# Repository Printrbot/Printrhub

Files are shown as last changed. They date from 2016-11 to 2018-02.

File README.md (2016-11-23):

# Printrhub

Welcome and thank you for your interest in our Printrhub technology. In this repository you will find everything you need to build upon the technology we invented. You may use the code and hardware to build your own devices or to improve your own Simple 2016. Please let us know about your projects and post issues or pull request to help us improve this project and code base.

## Purpose of the Printrhub

The Printrhub is the display component of our 3D printer Simple 2016 (http://printrbot.com/new-2016-simple/) and thus is the main user interface. The user can select, start, modify and pause prints or setup the printer with it. A fluid user interface controlled by touch as you know it from your smartphone let's anyone can start a print. The Hub also controls the printer and handles communication with the Printrbot cloud.

The Printrhub contains these components that form the final hardware

* ESP-12E module for WiFi connection and Over the Air updates
* MK20DX256LHV7 (Teensy 3) MCU is the main processor for handling the display, touch, SD card, controls the printer and ESP-12E
* 2.8 inch TFT display with 320x240 pixels
* Capacitive touch screen
* microSD card slot

As our board hosts two MCUs we need two different firmware, one for the ESP-12E module and the other one for the main MCU.

## Organization of this repository

* **/esp**: The firmware for the ESP-12E WiFi module
* **/mk20**: Contains the firmware for the main processor
* **/pcb**: Revisions 0.1, and 0.4 (final revision) of the PCB as Eagle and Copper files (for BOM and 3D views)
* **/utils**: The image tool that we use to build the ui.min file that contains all images used by the firmware combined in one file
* **/sdcard**: The initial content of the SD card that we ship with your printer (contains firmware images and root folder structure)
 
## Documentation
  
We have developed the hub in cooperation with Phillip Schuster (http://www.appfruits.com). He has written some documentation and behind the scenes reports that you should have read before working with our code and hardware.

### Behind the scenes of the Printrbot Simple 2016

How we started development and why we think you will learn something about product development in general.
http://www.appfruits.com/2016/11/behind-the-scenes-printrbot-simple-2016/

### Display System Explained

Expains the display and application framework in great detail. Explains the application flow, how to pseudo code multi threading and how implement a fast fluid and responsive user interface in a device capable of only 64 KB of RAM and 72 MHz.
http://www.appfruits.com/2016/11/printrbot-simple-2016-display-system-explained/

### CommStack explained

We invented CommStack to handle the communication between the MK20 and the ESP-12E module. It's fast, robust, bidirectional and features a nice request/response based system that enables two or more MCUs to communicate without having to handle all the little details.
http://www.appfruits.com/2016/11/printrbot-simple-2016-commstack-explained/

### Hardware explained

Describes the hardware in detail. Provides schematics, layout and details about the hardware we developed for the Printrbot hub.
http://www.appfruits.com/2016/11/printrbot-simple-2016-hardware-pcb-explained/

## Credits

Contains code or portions from these great libraries

* https://github.com/bakercp/PacketSerial
* https://github.com/PaulStoffregen/ILI9341_t3
* https://github.com/PaulStoffregen/ILI9341_fonts
* https://github.com/scanlime/esp8266-arm-swd
* https://github.com/esp8266/Arduino
* https://github.com/me-no-dev/ESPAsyncTCP.git
* https://github.com/me-no-dev/ESPAsyncWebServer.git
* https://github.com/bblanchon/ArduinoJson.git

Developed in cooperation with Phillip Schuster (@appfruits) from Appfruits (http://www.appfruits.com). Big thanks to Paul J. Stoffregen (https://www.pjrc.com/teensy/index.html) and his amazing Teensy project. It served as a great starting point and his amazing display driver for ILI9341 based display made our modern, fluid user interface possible.

## Support us

Printrbot invests time and resources providing this open source code, please support Printrbot and open-source hardware by purchasing products from Printrbot (http://www.printrbot.com)!

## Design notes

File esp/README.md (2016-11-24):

# Firmware for ESP-12E module

Printrhub consists of two MCUs on one board. The first is the well know ESP-8266 MCU, implemented as a ESP-12E module on the PCB. The second MCU is MK20DX256VLH7, better known as Teensy 3.1/3.2.

ESP is responsible for these features:

* Flashes MK20 MCU with latest firmware using ARMs SWD protocol
* Requests and downloads from the web
* Initial setup with WiFi and connecting your printer to the Printrbot Cloud

You will find the firmware for the ESP module on Printrhub board in this folder (esp). This is what you need to compile and install the firmware:

* Latest PlatformIO IDE (http://platformio.org)
* CLion (optional) (https://www.jetbrains.com/clion/)
* FTDI cable to transfer firmware to ESP module (for example this one https://www.sparkfun.com/products/9873)

## Getting started

Connect the FTDI header to the connection port marked FTDI on Printrhub and make sure it's connected in the right direction. If you use Sparkfuns FTDI breakout the IC on the breakout board should point to the Printrhub board.

## Uploading firmware to ESP

Before uploading the ESP firmware you will need to set ESP in DFU mode. You will need to do that before each upload cycle.

Press and hold the button named GPIO0 on the Printrhub board and press the RESET button on the Printrhub board. Release the GPIO0 button. The small LED on the bottom right side of the Printrhub should lightly dim now
indicating ESP is in DFU mode now.

## Using PlatformIO IDE to compile and upload ESP firmware

Download the latest PlatformIO IDE and install it. Open the esp folder in your PlatformIO IDE and compile the code. 

Make sure PlatformIO IDE uses the right USB connection (to the FTDI cable or breakout board) and upload the code. It will take some time.

## Using CLion to compile and upload ESP firmware

It's possible to use the awesome CLion IDE and we internally used that for development. CLion will use PlatformIO in the background but will seamlessly integrate it. You get a superior IDE but without the CMake hassle.
After you have installed PlatformIO and CLion open a terminal and navigate to this esp folder. Use this command to let PlatformIO setup a CLion IDE project for you.

`platformio init --ide clion --board esp12e`

Open the folder esp in CLion and you should have a nice, already setup project in CLion. Use the different targets available like PLATFORMIO_BUILD to compile the project and PLATFORMIO_UPLOAD to build and upload the project. 
Use the Build command to run the target process. Before uploading make sure your FTDI cable/breakout board is connected and ESP is in DFU mode (see above).

## Initial setup

If you applied the firmware you should see a new WiFi network named "Printrbot" on your phone or Mac/PC. Connect to that and open http://printrbot.local in your browser. You should see an initial setup screen
where you can enter your WiFi credentials of your local network.

Once that is done, ESP restarts and tries to connect to the local network. Wait a few minutes as ESP will detect that MK20 does not have a firmware installed and will automatically dowmload the latest MK20 firmware
from the web and flash MK20. After about 3-4 minutes Printrhub display will turn on and Printrhub is ready to explore

## Special considerations

ESP and MK20 use a direct connection based on UART and a custom protocol that we developed: CommStack. As CommStack uses the same Serial connection as FTDI cable uses to upload the firmware it's sometimes necessary to
 keep MK20 disabled while uploading the firmware. If you get strange upload errors and are sure ESP module is in DFU mode you have to short RESET_B (named RES_B on the Printrhub board) to GND. It's easy to do that as
 Printrhub has test points you can use to do that. If you do more constant development you should solder a wire to RES_B and GND and connect them together before uploading a firmware to ESP.
 
 MK20 detects if you want to upload a firmware to ESP by sensing the GPIO0 signal and stop any Serial communication through CommStack, but if MK20 firmware is not running correctly which can sometimes happen during 
 development you will have to stop it running.

## Support

There is no official support for this, but please drop an Issue and we'll have a look.

## License

Copyright (c) 2016 Printrbot Inc.

Permission is hereby granted, free of charge, to any person obtaining a copy of this software and associated documentation files (the "Software"), to deal in the Software without restriction, including without limitation 
the rights to use, copy, modify, merge, publish, distribute, sublicense, and/or sell copies of the Software, and to permit persons to whom the Software is furnished to do so, subject to the following conditions:

The above copyright notice and this permission notice shall be included in all copies or substantial portions of the Software.

THE SOFTWARE IS PROVIDED "AS IS", WITHOUT WARRANTY OF ANY KIND, EXPRESS OR IMPLIED, INCLUDING BUT NOT LIMITED TO THE WARRANTIES OF MERCHANTABILITY, FITNESS FOR A PARTICULAR PURPOSE AND NONINFRINGEMENT. IN NO EVENT SHALL THE 
AUTHORS OR COPYRIGHT HOLDERS BE LIABLE FOR ANY CLAIM, DAMAGES OR OTHER LIABILITY, WHETHER IN AN ACTION OF CONTRACT, TORT OR OTHERWISE, ARISING FROM, OUT OF OR IN CONNECTION WITH THE SOFTWARE OR THE USE OR OTHER DEALINGS IN THE SOFTWARE.

## Credits

Contains code or portions from these great libraries

* https://github.com/scanlime/esp8266-arm-swd
* https://github.com/bakercp/PacketSerial
* https://github.com/esp8266/Arduino
* https://github.com/me-no-dev/ESPAsyncTCP.git
* https://github.com/me-no-dev/ESPAsyncWebServer.git
* https://github.com/bblanchon/ArduinoJson.git

Developed in cooperation with Phillip Schuster (@appfruits) from Appfruits (http://www.appfruits.com).

## Support us

Printrbot invests time and resources providing this open source code, please support Printrbot and open-source hardware by purchasing products from Printrbot (http://www.printrbot.com)!

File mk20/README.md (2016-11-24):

# Firmware for MK20DX256LHV7 (Teensy 3.x) MCU

Printrhub consists of two MCUs on one board. The first is the well know ESP-8266 MCU, implemented as a ESP-12E module on the PCB. The second MCU is MK20DX256VLH7, better known as Teensy 3.1/3.2.

Teensy MCU is responsible for these features:

* Reads and writes from SD card
* Controls Display, Touch and printer
* Communicates with ESP-12E module to download project index files and G-Codes from Printrbot cloud

You will find the firmware for the MCU on Printrhub board in this folder (mk20). This is what you need to compile and install the firmware:

* Latest PlatformIO IDE (http://platformio.org)
* CLion (optional) (https://www.jetbrains.com/clion/)
* Segger J-LINK or similar SWD compatible debug probe

## Documentation

One of our team members has written an extensive documentation and behind the scenes report about the development of the Printrbot Simple 2016. We advise you to read this before digging into this code to give you some context and advise.

### Behind the scenes of the Printrbot Simple 2016

How we started development and why we think you will learn something about product development in general.
http://www.appfruits.com/2016/11/behind-the-scenes-printrbot-simple-2016/

### Display System Explained

Expains the display and application framework in great detail. Explains the application flow, how to pseudo code multi threading and how implement a fast fluid and responsive user interface in a device capable of only 64 KB of RAM and 72 MHz.
http://www.appfruits.com/2016/11/printrbot-simple-2016-display-system-explained/

### CommStack explained

We invented CommStack to handle the communication between the MK20 and the ESP-12E module. It's fast, robust, bidirectional and features a nice request/response based system that enables two or more MCUs to communicate without having to handle all the little details.
http://www.appfruits.com/2016/11/printrbot-simple-2016-commstack-explained/

### Hardware explained

Describes the hardware in detail. Provides schematics, layout and details about the hardware we developed for the Printrbot hub.
http://www.appfruits.com/2016/11/printrbot-simple-2016-hardware-pcb-explained/

## Using PlatformIO IDE to compile MK20 firmware

Download the latest PlatformIO IDE and install it. Open the mk20 folder in your PlatformIO IDE and compile the code. 

## Uploading firmware

There are two options to upload new firmware to the device:

* Using existing over the air update mechanism (see ESP firmware in this repository)
* SWD compatible ARM debug probe (like Segger J-LINK) to upload code via Serial Wire Debug (SWD)
  
### Over the Air updates
  
  If you don't have the necessary hardware (debug probe) to upload code via SWD then this is the easiest method. You will need to modify the ESP firmware. This is an excerpt of the file web_server.cpp and sets up a GET request that is watching for a /update_mk20 event and starts a firmware update. 
  
  ```
    webserver.addOptionsRequest("/update_mk20");
    server.on("/update_mk20", HTTP_GET, [](AsyncWebServerRequest *request) {
  	String mk20FirmwareFile("/mk20.bin");
  	FirmwareUpdateInfo *updateInfo = Application.getFirmwareUpdateInfo();
  	if (updateInfo != NULL) {
  	  DownloadFileToSPIFFs *downloadMK20Firmware = new DownloadFileToSPIFFs(updateInfo->mk20_url, mk20FirmwareFile);
  	  MK20FirmwareUpdate *mk20UpdateFirmware = new MK20FirmwareUpdate(mk20FirmwareFile);
  	  downloadMK20Firmware->setNextMode(mk20UpdateFirmware);
  	  Application.pushMode(downloadMK20Firmware);
  	  request->send(200, "text/plain", "\nupdate of MK20 started, please wait...\n\n");
  	} else {
  	  request->send(200, "text/plain", "\nupdate of MK20 failed, please wait until firmware data have been loaded and try again...\n\n");
  	}
    });
  ```
  
  However, this code loads the firmware provided by the Printrbot Cloud. You will want to user your own binary file. Best way is to modify it this way:
   
     ```
       webserver.addOptionsRequest("/update_mk20");
       server.on("/update_mk20", HTTP_GET, [](AsyncWebServerRequest *request) {
     	String mk20FirmwareFile("/mk20.bin");
     	FirmwareUpdateInfo *updateInfo = Application.getFirmwareUpdateInfo();
     	if (updateInfo != NULL) {
     	  DownloadFileToSPIFFs *downloadMK20Firmware = new DownloadFileToSPIFFs("http://WWW.YOURDOMAIN.COM/YOURFIRMWARE.BIN", mk20FirmwareFile);
     	  MK20FirmwareUpdate *mk20UpdateFirmware = new MK20FirmwareUpdate(mk20FirmwareFile);
     	  downloadMK20Firmware->setNextMode(mk20UpdateFirmware);
     	  Application.pushMode(downloadMK20Firmware);
     	  request->send(200, "text/plain", "\nupdate of MK20 started, please wait...\n\n");
     	} else {
     	  request->send(200, "text/plain", "\nupdate of MK20 failed, please wait until firmware data have been loaded and try again...\n\n");
     	}
       });
     ```
     
     This will use the standard over the air updates but will use the URL you provide to flash MK20.
     
The workflow would be this:
     
     * Compile MK20 firmware and generate a bin file from the hex file (see hextobin.sh) for details on how to do that
     * Upload your firmware binary to your own webspace or local webserver
     * Modify ESP firmware and flash ESP
     * Load this URL in your browser to receive some helful logs (http://IPADDRESS_OF_PRINTER/events)
     * Start up your printer and call this URL in your browser (http://IPADDRESS_OF_PRINTER/update_mk20)
     * ESP will download your firmware and install it. Your display will turn off.
     
### Uploading code via SWD
      
If you want to upload via SWD connect your probe to SWD_IO, SWD_CLK, GND and RESET_B. You will also need to connect your VREF to 3.3V. This way your debug probe can sense the correct logic level. See your manual for details on the procedure. All necessary signals are exposed in the test points in the middle of the board.

## Using CLion to compile and upload ESP firmware

It's possible to use the awesome CLion IDE and we internally used that for development. CLion will use PlatformIO in the background but will seamlessly integrate it. You get a superior IDE but without the CMake hassle. After you have installed PlatformIO and CLion open a terminal and navigate to this mk20 folder. Use this command to let PlatformIO setup a CLion IDE project for you.

`platformio init --ide clion`

Open the folder mk20 in CLion and you should have a nice, already setup project in CLion. Use the different targets available like PLATFORMIO_BUILD to compile the project. Use the Build command to run the target process. 

You will need 2016.2 or the latest 2016.3 of CLion for remote debugging via SWD. 

## Support

There is no official support for this, but please drop an Issue and we'll have a look. If you find bugs or add enhancements, please let us know and send a pull request.

## License

Copyright (c) 2016 Printrbot Inc.

Permission is hereby granted, free of charge, to any person obtaining a copy of this software and associated documentation files (the "Software"), to deal in the Software without restriction, including without limitation 
the rights to use, copy, modify, merge, publish, distribute, sublicense, and/or sell copies of the Software, and to permit persons to whom the Software is furnished to do so, subject to the following conditions:

The above copyright notice and this permission notice shall be included in all copies or substantial portions of the Software.

THE SOFTWARE IS PROVIDED "AS IS", WITHOUT WARRANTY OF ANY KIND, EXPRESS OR IMPLIED, INCLUDING BUT NOT LIMITED TO THE WARRANTIES OF MERCHANTABILITY, FITNESS FOR A PARTICULAR PURPOSE AND NONINFRINGEMENT. IN NO EVENT SHALL THE 
AUTHORS OR COPYRIGHT HOLDERS BE LIABLE FOR ANY CLAIM, DAMAGES OR OTHER LIABILITY, WHETHER IN AN ACTION OF CONTRACT, TORT OR OTHERWISE, ARISING FROM, OUT OF OR IN CONNECTION WITH THE SOFTWARE OR THE USE OR OTHER DEALINGS IN THE SOFTWARE.

## Credits

Contains code or portions from these great libraries

* https://github.com/bakercp/PacketSerial
* https://github.com/PaulStoffregen/ILI9341_t3
* https://github.com/PaulStoffregen/ILI9341_fonts

Developed in cooperation with Phillip Schuster (@appfruits) from Appfruits (http://www.appfruits.com).

## Support us

Printrbot invests time and resources providing this open source code, please support Printrbot and open-source hardware by purchasing products from Printrbot (http://www.printrbot.com)!

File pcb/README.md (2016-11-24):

# Printrhub PCB

This repository contains two revisions of the PCB of the Printrhub. See main folder for more details about the project.

## Documentation and details

This PCB has been developed in cooperation by Phillip Schuster (http://www.appfruits.com). He has written a blog post about these PCBs and documents the details of it.
http://www.appfruits.com/2016/11/printrbot-simple-2016-hardware-pcb-explained/

## Revisions

This folder contains two revisions:

### Revision 0.1

This has been the first PCB we have created and contains the Teensy bootloader chip and an USB port that makes it easy to flash new firmware. It's basically just a bigger Teensy with more components. The firmware supports this revision, but you will need to set the correct #define in the HAL.h file in both firmwares

### Revision 0.4

This is the final revision we ship with the Simple 2016. Firmware must be flashed via SWD or our Over the Air update system.

## EAGLE and Copper files

These files can be opened with EAGLE, but you will need at least a Hobbyist license as we use 4-layers. We have also added Copper (http://www.copper-app.com) files that contain the complete BOM and a 3D view of the boards.

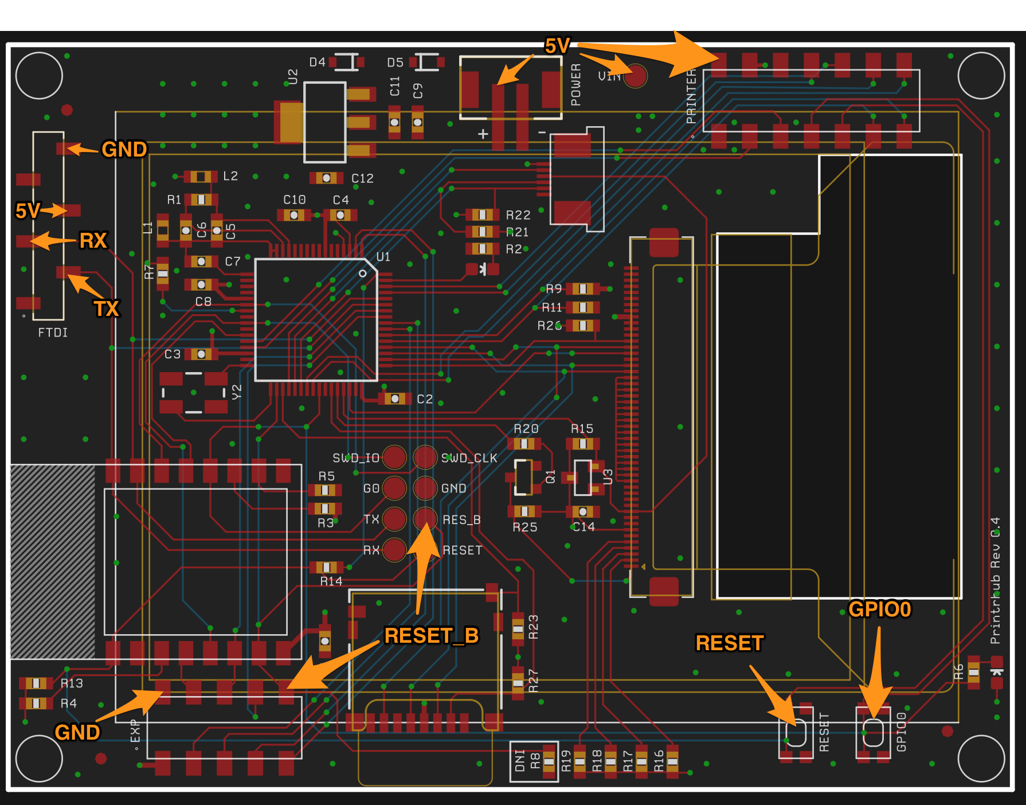
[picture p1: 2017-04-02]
Signals.png

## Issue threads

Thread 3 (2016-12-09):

Info button / display settings for part preview

ururk, 2016-12-09:
Currently, the only way to know what the settings are for a part on the printer is to hit print - it would be useful to have an info button that displays the basic information for a part (essentially, whatever options are configurable), including print time and filament quantity. An uncluttered preview is nice - hence an info button. The current UI is nicely done, and this is just a suggestion.

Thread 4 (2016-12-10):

add git tags for firmware release numbers.

bmv437, 2016-12-10:
Hi there. I can see that my printrhub has firmware package 108, but I'm not sure at what commit that firmware package was built. Is it possible to add git tags so we can keep track of what code gets shipped in which firmware build?

```json
{
    "firmware": 108,
    "fw_cloud_buildnr": 108,
    "fw_info_sent": true,
    "fw_update": true,
    "ipaddress": "192.168.1.10",
    "locked": false,
    "mk20": true,
    "name": "printrbot",
    "serialnr": "",
    "softapip": "0.0.0.0",
    "ssid": "myWifi"
}
```

Thanks!

bmv437, 2016-12-10:
So it looks like the cloud firmware version is 108, but in this repo it's version 106 (at least that's what the header files say)

https://github.com/Printrbot/Printrhub/blob/master/esp/src/config.h#L35
https://github.com/Printrbot/Printrhub/blob/master/mk20/src/framework/core/Application.h#L65

Is this the latest code running on the PrinterHub? or did `FIRMWARE_BUILDNR` just not get updated?

mickbalaban, 2016-12-10:
Hey Brandon, the reason for this version not matching the one that is deployed on printers is that we were transitioning from private repo with multiple branches, into this one. Phillip was working on preparing the repo for release, and in the meantime I pushed a new firmware update that had few bug fixes.

I will merge the code asap and make sure everything compiles correctly and then it will be up to date. Feature that is missing in this repo is addition of Light control. Previously we had "update" button in control panel, which was removed and replaced with light.

mickbalaban, 2016-12-12:
ok, code should be now in sync with old repo. All future updates will be done in this repo going forward...

mickbalaban, 2016-12-12:
repo is now tagged. Please reopen if you see any other issues.

Closed 2016-12-12.

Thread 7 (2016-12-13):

Load filament workflow - include unload?

ururk, 2016-12-13:
When I go to change filament, it would be nice if the load filament workflow could include an unload step:

* Heat extruder
* Question prompt: "Is filament already loaded??"
  * If `Yes`, proceed to unload filament
* Once done, resume standard load process

Right now this is a two-step process, which includes two extruder heat-up times.

mickbalaban, 2016-12-13:
Thanks for your suggestion, but I disagree that your what you proposed is better user experience. Currently you are prompted to either load or unload filament. If you unload it first, and then click on load filament, hotend is not cooled off completely, so second time it will take less time to heat up. Still very simple.. one click, one action.

What you are proposing is that instead of selecting "load" or "unload", we do one "change filament" action, heat the hotend, then ask user if they want to load or unload. Now we went from one click to two clicks for something we needed only one before.

You are also assuming that user wants to change filament, which may be wrong. What if they just want to remove the roll of filament and store it in container after printing? With your approach, they would unload the filament, then printer will go into load filament after that, so they will have to cancel out of it. Again, adding clicks and making it more complicated.

Sorry, but I am not convinced that this is better then existing way of doing it.

ururk, 2016-12-13:
True. Though I wasn't suggesting removing the unload filament step - I suppose this suggestion would require a third option (Change Filament), which could be confusing since the other steps would still be present. I guess I want it both ways - load/unload as distinct steps, and a change option. Feel free to close this suggestion out.

mickbalaban, 2016-12-13:
no worries. We ran scenarios like this when we were designing the interface and tried to minimize user clicks with each action. Our choices may not have been the best so please feel free to continue to submit suggestions, and even better, start playing with the code :)
Ill keep this open to see if anybody else has any opinion on this.

ururk, 2016-12-13:
Thanks - good to know. I really like the simplicity of the setup, and it prevents people from getting confused when they go to do something.

As for playing around with the code - wish I had the time!

Closed 2017-02-14.

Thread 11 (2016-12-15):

Printer WIFI page time limit?

brookdrumm, 2016-12-15:
Since nothing can be downloaded to the printer when it is on the WIFI screen, perhaps one work around is to implement a 10 second timer to revert back to the previous page - or the main Projects page.

This would avoid people THINKING they are sending files to the printer, when in reality, IF they are on the WIFI screen, it just silently fails.  Instead of explaining it, this would all but eliminate a file upload failure due to being on that one restrictive screen.

There are other ways to solve this, but not sure of the limitations you are dealing with:
-allow uploads on that page
-explain with onscreen words "No uploads allowed in this screen"
-Having printrbot.cloud warn if they are on that black-magical screen (complicated)
--??

mickbalaban, 2017-02-14:
fixed

Closed 2017-02-14.

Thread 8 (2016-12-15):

Enter / Edit WIFI name and password on printer

brookdrumm, 2016-12-15:
Please add an edit button on the wifi screen to enter wifi name and password.

I realize we your current soft-keyboard does not support all characters, but for most, this would be quite helpful.

I believe this is the most straight forward approach for the majority of people out there to connect to local wifi

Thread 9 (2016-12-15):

Report MAC address on WIFI screen

brookdrumm, 2016-12-15:
On wifi screen, please report the MAC address.

this would assist those requiring MAC address to add printer to their network.

The MAC address could also be reported in the main screen on the ESP (currently the default page  when you hit the IP address of the printer http://192.168.4.1 for example)

pschuster, 2017-02-24:
Mac address is now evaluated and saved in SystemSettings and transferred to MK20 where it is displayed in the settings screen.

pschuster, 2017-02-24:
Mac Address is displayed in setup screen.
@mickbalaban: Your turn to make it more pretty if needed.

brookdrumm, 2017-02-24:
Awesome!

Sent from my iPhone

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

Closed 2017-02-24.

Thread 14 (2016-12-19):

Display/Indicate currently selected filament

ururk, 2016-12-19:
After switching filament types (PLA -> Ninjaflex), there is no indication what filament type is being printed with. Some ideas:

* Green check mark indicating a specific filament is selected as the current material
* On the printing screen, indicate which filament is selected
* On the filament picker screen, have the first choice be the selected filament type and use the words "Current Filament"
* A persistent "Material: Name" on relevant screens (load/unload, print, etc...)

I've been switching between a few different filament types, and think it would be useful to know what filament the printer currently thinks it is using. Also, I'm guessing it always reverts to the first filament in the list after rebooting, but I don't actually know.

mickbalaban, 2017-02-14:
Added "selected" message instead of select button on material screen when current filament is displayed.  Also added material message to the print status scene (replacing inaccurate time estimate)

https://github.com/Printrbot/Printrhub/commit/fc4516317c4d3a1840bdff1b44222dd81d090bee
https://github.com/Printrbot/Printrhub/commit/f8f0ae3401f5a255a8c80860f8724f0b174dc480

Closed 2017-02-14.

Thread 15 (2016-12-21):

Capture actual print times and adjust estimate accordingly

ururk, 2016-12-21:
Feel free to ignore this suggestion, but it occurred to me...

Time estimates will always be off. They take longer than what the slicer (or in our case, the 2016 Simple) says they will take. For the Simple I haven't quantified how far they are off, but they do not seem to be accurate. The printrhub isn't at fault, since this comes from the cloud. I've printed both PLA (100% speed) and flexible filament (50% speed).

However, if there was a checksum for both prints and filament, a data table could be constructed with:

    Model checksum, Selected Filament profile checksum, Actual print time

* Anytime the model is deleted or updated, erase all rows with the old model checksum
* Anytime a specific filament profile is deleted or updated, erase all rows with the old filament checksum
* A new row would be added when the print finished, or updated (and averaged) if a row already existed
* When printing, if the checksums match up, use this actual print time instead of estimated

mickbalaban, 2017-02-13:
we decided to remove estimated print time from the print screen since it was not very accurate. We may add this feature back in when we have a better implementation.

https://github.com/Printrbot/Printrhub/commit/6a3a4a97bd44ad0d5bfb6b0256bbe7bd95d63e87

Closed 2017-02-13.

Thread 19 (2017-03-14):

Attempting to print model produces "Unknown Error" or "File Not Found"

pr3sidentspence, 2017-03-14:
1. Import project from thingiverse
2. Send to printer
3. Select part and tap print
4. Shows downloading briefly
5. Get error on screen. Either "Unknown Error" or "File Not Found"

I can't say that I've seen this from manually uploaded STLs, but I might have. I haven't done this much yet.

wjsteele, 2017-10-19:
This appears to be a slicing failure.  Go to the printrbot.cloud page and look to see if the filename is in red... if it is, then the slicer failed for some reason... most likely it is outside the limits of the print area.  Scale or move the part so that it is within the printable envelope and try again.  (I deleted the old jobs from the printer and re-loaded them after I fix the object.)

pr3sidentspence, 2017-10-20:
Hmm. I don't think that was the case for me.

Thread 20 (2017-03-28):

UI prompts user to load/unload filament before the print head has moved up and forward.

pr3sidentspence, 2017-03-28:
If one were to attempt to load the filament when first prompted, they could potentially be hurt by fast moving head.

sfcgeorge, 2017-10-14:
Yeah this whole process seemed weird to me.

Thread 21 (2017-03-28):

Extruder ran backwards when running LOAD filament

pr3sidentspence, 2017-03-28:
1) Use on-screen UI to *load* filament
2) Extruder retracted instead

This repeated until I power cycled.
The screen said Load filament now.

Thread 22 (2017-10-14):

Load filament doesn't run extruder

sfcgeorge, 2017-10-14:
I used the on-screen load filament command, extruder heated, the print head moved, but the extruder didn't turn it just said load filament now. I assume the extruder is meant to turn to help you load the filament? In Brook's video he implies this.

pr3sidentspence, 2017-10-20:
It should, yes. Sometimes, if you're really naughty, it runs backward during the load.

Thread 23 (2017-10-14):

First boot dodgy

sfcgeorge, 2017-10-14:
On first boot I did the load filament thing, it said heating extruder but nothing happened. There was a picture showing red lights but the lights never came on. After 5 minutes I gingerly touched the hot end and it was cold. After a reboot the lights came on and the hot end did heat.

One issue is that to go wrong the first time it's turned on is a bad first impression.

Secondly it's not even clear when it has gone wrong - the screen was working fine, there was no message to say anything was wrong, but the lights and heat didn't come on.

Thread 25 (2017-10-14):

Z maxes out at end of print causing jam

sfcgeorge, 2017-10-14:
I'm using the small starter spool you ship with the printer. When a print finishes the gantry whizzes up the Z at warp speed, crashes into the spool, jams and causes a horrible grinding noise from the stepper as it skips!

The spool naturally gets pulled to the left past where it's supposed to be because those mini spools have a weird lip in the middle but not at the sides so there's nothing to stop it from sliding over too far.

Don't have the gantry go so high, or ship the mini spools with printed inserts that add a lip to the outside so it doesn't slide over, or make the flange on the spool handle bigger.

sfcgeorge, 2017-10-20:
Maybe it isn't the Printrhub doing this but the end Gcode. It only seems to happen with the default calibration cuboid print, the others don't move up at the end.

ururk, 2017-12-19:
I designed a little add-on to prevent this from happening:

https://www.thingiverse.com/thing:1954463

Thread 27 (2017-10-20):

High speed head crash into bed

sfcgeorge, 2017-10-20:
Mid way through a Cura USB print I noticed it wasn't coming out well so I clicked "Abort" in Cura, which for some reason rams the print head into the bed at high speed and didn't stop until I powered off. This of course ruined the PEI tape :(

I realise this is probably a Cura issue, perhaps because on Ultimakers the bed goes down rather than the gantry.

But surely the Printrboard firmware should disallow commands that send the print head below the minimium Z. It homes at the start of the print and does bed levelling, so it knows where the bed is, I don't see why you'd let it smash through that.

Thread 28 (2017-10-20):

Crunking out X after homing

sfcgeorge, 2017-10-20:
When doing a USB print from Cura the printer homed correctly, and then for some reason the X axis decided to keep going right (- past home) causing the motor to click until powered off.

Weird bug, I don't know why after homing the printer would allow itself to go negative on the X.

It only happened once. After a power cycle and not changing any print settings the next attempt worked fine.

(More a G2 issue but I don't see a PB fork of G2)

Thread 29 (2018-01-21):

Enabling heatbed associated with materials in the cloud

pschuster, 2018-01-21:
If heatbed is activated it should heat up along the nozzle. Printing should start once both the nozzle and the heatbed have reached desired temperature.

There might be printers that have no heatbed installed. In this case we must either sense if there is a heatbed available and exclude that in the preheat phase or we must make sure that fireware does not wait for the heatbed to reach temperature when we only receive 0 degrees value back from printer status.

Questions:
* Is there a way to sense if a heatbed is installed (perhaps g2 could send that in the status response)

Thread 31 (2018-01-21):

Option to add SSID and password on touch screen??

pschuster, 2018-01-21:
Setting up the printer via touch screen only should be possible without external device support (i.e. launching a browser on your PC/Mac or smartphone to setup the printer).

The currently implemented keyboard only supports various symbols and special characters. But perhaps those are not enough if users use a wide range of symbols and special characters in their WiFi passwords.

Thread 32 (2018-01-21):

List network IP address at all times

pschuster, 2018-01-21:
The display should display the printers IP address all the time or if not possible should be easily accessibly with a tap on a button.

pschuster, 2018-01-21:
We could use the sidebar to show a WiFi symbol and by tapping on that we show the IP address in a small popup window like we do with alert messages.

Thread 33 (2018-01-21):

Prompt “update firmware” when new firmware is available

pschuster, 2018-01-21:
This could remove requirement of using the cloud firmware update page— which is difficult to use and confusing. That page could be used as a last ditch effort btw

pschuster, 2018-01-21:
This should already work. We should examine why the current implementation does not work.

ESP loads the firmware.json file and sets firmware application info in local data structure. Later on it examines the firmware and compares to current settings once MK20 responded on the ping signal with current firmware version number.

Please have a look to this code: https://github.com/Printrbot/Printrhub/blob/808b6a5a75406fa9f20b1923346427c52aa1929c/esp/src/application.cpp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

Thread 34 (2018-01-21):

Display “updating firmware, do not shut off power” instead of screen going black

pschuster, 2018-01-21:
(May not be possible), in which case, we could give instructions to not turn off screen before update begins.

pschuster, 2018-01-21:
MK20 controls the display and RESET signal of display is connected to reset signal of the display. During flashing MK20 the display is turned off. I hacked the board by having a pull up resistor on the display reset signal (its a pull down resistor at the moment) which causes the display to be turned on but just showing a plain white screen which is better.

We could test that again and fix the boards in the next production run.

In the meantime we can add that screen.

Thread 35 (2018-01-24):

Document G-Codes used in current firmware

pschuster, 2018-01-24:
G-Codes are hardcoded in the firmware (see Printr.cpp). This has issues with sending files via WiFi and for overall flexibility.

As a first step we should document current G-Codes used and then decide where to split them or where to implement them. Documentation is required in [Wiki](https://github.com/Printrbot/Printrhub/wiki/G-Codes)

There are various possibilities:

1) Keep them in the firmware as is (hard coded)
2) G-Codes downloaded from the Cloud contain all G-Codes (i.e. G-Codes are generated in the cloud)
3) G-Codes are stored on internal SD card.
4) ...

## Tasks
- [ ] Document G-Codes used in current firmware
- [ ] Discuss and decide where to put them (in this issue)
- [ ] Create issues required for refactoring

oddirmeyer, 2018-01-25:
Starting G-code descriptions updated and ready for review.

pschuster, 2018-01-25:
Awesome. Thank you very much. That makes things easier I think. The next step would be to cluster those G-Codes in basic setup, and print preparation or should we do things like reset x and y and probing before each print?

abdrumm, 2018-04-04:
I am ok w minimum viable product that works ;) so we don’t HAVE to do it before every print. I think since all printers probe before print, it’s just best practice... conservative but not necessary

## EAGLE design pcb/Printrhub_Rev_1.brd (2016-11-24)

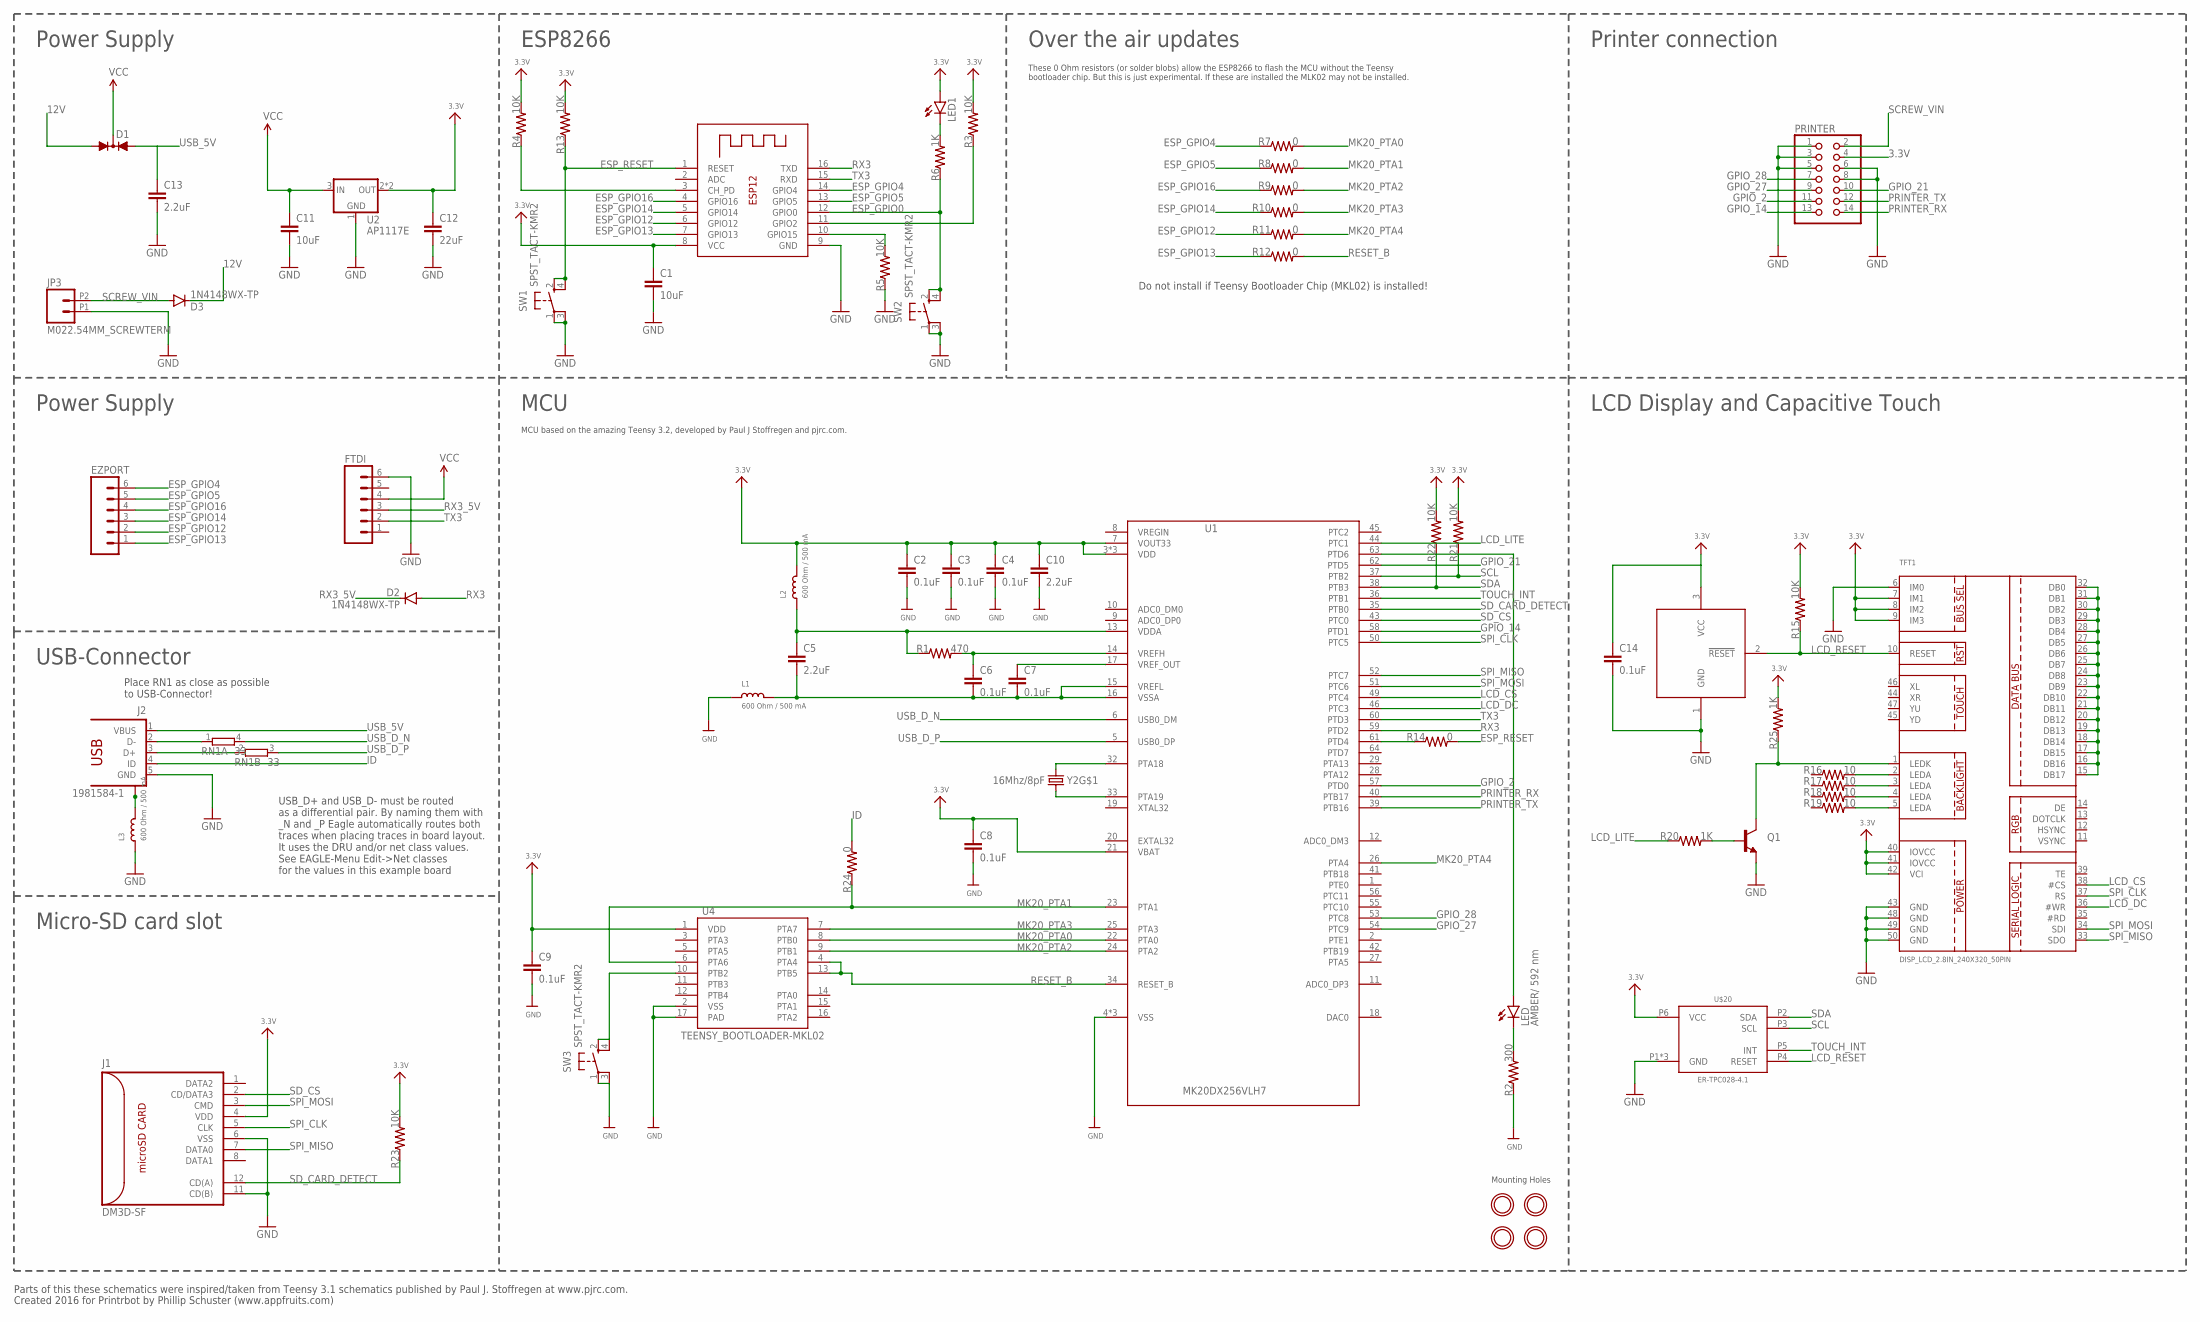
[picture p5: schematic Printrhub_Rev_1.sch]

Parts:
C1, C11: 10uF; 0603-CAP
C2, C3, C4, C6, C7, C8, C9, C14: 0.1uF; 0603-CAP
C5, C10, C13: 2.2uF; 0603-CAP
C12: 22uF; 0603-CAP
D1: DIODE-2AC|CASOT23; SOT23
D2, D3: 1N4148WX-TP; SOD-323; MPN 1N4148WX-TP
EZPORT: M06SMD-STRAIGHT; 1X06_SMD_STRAIGHT
FTDI: M06SMD-STRAIGHT; 1X06_SMD_STRAIGHT
J1: DM3D-SF
J2: 1981584-1
JP3: M022.54MM_SCREWTERM; 1X02_2.54_SCREWTERM
L1, L2, L3: 600 Ohm / 500 mA; 0603
LED: AMBER/ 592 nm; LED-0603
LED1: LED-GREEN; LED-0603
PRINTER: PINHD-2X7SMT; 2X07_SMT
Q1: TRANSISTOR_NPNSOT23-3; SOT23-3
R1: 470; 0603-RES
R2: 300; 0603-RES
R3, R4, R5, R13, R15, R21, R22, R23: 10K; 0603-RES
R6, R20, R25: 1K; 0603-RES
R7, R8, R9, R10, R11, R12, R14, R24: 0; 0603-RES
R16, R17, R18, R19: 10; 0603-RES
RN1: 33; EXB34V; MPN EXB-34V330JV
SW1, SW2, SW3: SPST_TACT-KMR2; KMR2
TFT1: DISP_LCD_2.8IN_240X320_50PIN; TFT_2.83IN_240X320_50PIN
U1: MK20DX256VLH7; MPN MK20DX256VLH7
U2: AP1117E; SOT223
U3: MAX308-SOT23; SOT23
U4: TEENSY_BOOTLOADER-MKL02; QFN50P300X300X100-17N
U$15, U$16, U$17, U$18: MOUNTINGHOLE2.0; MOUNTINGHOLE_2.0_PLATED
U$20: ER-TPC028-4.1; ER-CON06HB-1
X1: ESP-12
Y2: 16Mhz/8pF; CRYSTAL-SMD-5X3; MPN ECS-160-8-30B-CKM

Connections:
3.3V: C1.1, C2.1, C3.1, C4.1, C8.1, C9.1, C10.1, C12.1, C14.1, J1.4 (VDD), L2.2, LED1.A, PRINTER.4, R3.2, R4.2, R13.2, R15.2, R21.2, R22.2, R23.2, R25.2, TFT1.7 (IM1), TFT1.8 (IM2), TFT1.9 (IM3), TFT1.40 (IOVCC), TFT1.41 (IOVCC), TFT1.42 (VCI), U1.3 (VDD), U1.7 (VOUT33), U1.21 (VBAT), U1.30 (VDD), U1.48 (VDD), U2.2 (OUT), U2.4 (OUT), U3.3 (VCC), U4.1 (VDD), U$20.P6 (VCC), X1.8 (VCC)
12V: D1.1 (A1), D3.C
ESP_GPIO0: R6.1, SW2.2 (S), SW2.4 (S1), X1.12 (GPIO0)
ESP_GPIO4: EZPORT.6, R7.1, X1.14 (GPIO4)
ESP_GPIO5: EZPORT.5, R8.1, X1.13 (GPIO5)
ESP_GPIO12: EZPORT.2, R11.1, X1.6 (GPIO12)
ESP_GPIO13: EZPORT.1, R12.1, X1.7 (GPIO13)
ESP_GPIO14: EZPORT.3, R10.1, X1.5 (GPIO14)
ESP_GPIO16: EZPORT.4, R9.1, X1.4 (GPIO16)
ESP_RESET: R13.1, R14.2, SW1.2 (S), SW1.4 (S1), X1.1 (RESET)
GND: C1.2, C2.2, C3.2, C4.2, C8.2, C9.2, C10.2, C11.2, C12.2, C13.2, C14.2, FTDI.6, J1.6 (VSS), J1.11 (CD(B)), J2.5 (GND), JP3.P1 (1), L1.1, L3.1, PRINTER.1, PRINTER.3, PRINTER.5, PRINTER.6, PRINTER.8, Q1.2 (E), R2.1, R5.1, SW1.1, SW1.3 (P1), SW2.1, SW2.3 (P1), SW3.1, SW3.3 (P1), TFT1.6 (IM0), TFT1.43 (GND), TFT1.48 (GND), TFT1.49 (GND), TFT1.50 (GND), U1.4 (VSS), U1.31 (VSS), U1.47 (VSS), U2.1 (GND), U3.1 (GND), U4.2 (VSS), U4.17 (PAD), U$20.P1 (GND), U$20.PAD@0 (GND), U$20.PAD@1 (GND), X1.9 (GND)
GPIO_2: PRINTER.11, U1.57 (PTD0)
GPIO_14: PRINTER.13, U1.58 (PTD1)
GPIO_21: PRINTER.10, U1.62 (PTD5)
GPIO_27: PRINTER.9, U1.54 (PTC9)
GPIO_28: PRINTER.7, U1.53 (PTC8)
ID: J2.4 (ID), R24.2
LCD_CS: TFT1.38 (#CS), U1.49 (PTC4)
LCD_DC: TFT1.36 (#WR), U1.46 (PTC3)
LCD_LITE: R20.1, U1.44 (PTC1)
LCD_RESET: R15.1, TFT1.10 (RESET), U3.2 (!RESET), U$20.P4 (RESET)
MK20_PTA0: R7.2, U1.22 (PTA0), U4.8 (PTB0)
MK20_PTA1: R8.2, R24.1, U1.23 (PTA1), U4.6 (PTA6)
MK20_PTA2: R9.2, U1.24 (PTA2), U4.9 (PTB1)
MK20_PTA3: R10.2, U1.25 (PTA3), U4.7 (PTA7)
MK20_PTA4: R11.2, U1.26 (PTA4)
unnamed: R3.1, X1.11 (GPIO2)
unnamed: R4.1, X1.3 (CH_PD)
unnamed: R5.2, X1.10 (GPIO15)
unnamed: LED1.C, R6.2
unnamed: R14.1, U1.61 (PTD4)
unnamed: Q1.3 (C), R25.1, TFT1.1 (LEDK)
unnamed: R16.2, TFT1.2 (LEDA)
unnamed: LED.A, U1.63 (PTD6)
unnamed: R17.2, TFT1.3 (LEDA)
unnamed: R18.2, TFT1.4 (LEDA)
unnamed: R19.2, TFT1.5 (LEDA)
unnamed: Q1.1 (B), R20.2
unnamed: TFT1.15 (DB17), TFT1.16 (DB16), TFT1.17 (DB15), TFT1.18 (DB14), TFT1.19 (DB13), TFT1.20 (DB12), TFT1.21 (DB11), TFT1.22 (DB10), TFT1.23 (DB9), TFT1.24 (DB8), TFT1.25 (DB7), TFT1.26 (DB6), TFT1.27 (DB5), TFT1.28 (DB4), TFT1.29 (DB3), TFT1.30 (DB2), TFT1.31 (DB1), TFT1.32 (DB0)
unnamed: LED.C, R2.2
unnamed: U1.32 (PTA18), Y2.3 (2)
unnamed: U1.33 (PTA19), Y2.1
PRINTER_RX: PRINTER.14, U1.40 (PTB17)
PRINTER_TX: PRINTER.12, U1.39 (PTB16)
PROGRAM: SW3.2 (S), SW3.4 (S1), U4.10 (PTB2)
RESET_B: R12.2, U1.34 (RESET_B), U4.4 (PTA4), U4.13 (PTB5)
RX3: D2.A, U1.59 (PTD2), X1.16 (TXD)
RX3_5V: D2.C, FTDI.3
SCL: R21.1, U1.37 (PTB2), U$20.P3 (SCL)
SCREW_VIN: D3.A, JP3.P2 (2), PRINTER.2
SDA: R22.1, U1.38 (PTB3), U$20.P2 (SDA)
SD_CARD_DETECT: J1.12 (CD(A)), R23.1, U1.35 (PTB0)
SD_CS: J1.2 (CD/DATA3), U1.43 (PTC0)
SPI_CLK: J1.5 (CLK), TFT1.37 (RS), U1.50 (PTC5)
SPI_MISO: J1.7 (DATA0), TFT1.33 (SDO), U1.52 (PTC7)
SPI_MOSI: J1.3 (CMD), TFT1.34 (SDI), U1.51 (PTC6)
TOUCH_INT: U1.36 (PTB1), U$20.P5 (INT)
TX3: FTDI.2, U1.60 (PTD3), X1.15 (RXD)
USB_5V: C13.1, D1.2 (A2), J2.1 (VBUS)
USB_CON_N: J2.2 (D-), RN1.1
USB_CON_P: J2.3 (D+), RN1.2 (1)
USB_D_N: RN1.4 (2), U1.6 (USB0_DM)
USB_D_P: RN1.3 (2), U1.5 (USB0_DP)
USB_SHIELD: J2.S1, J2.S2, J2.S3, J2.S4, L3.2
VCC: C11.1, D1.3 (C), FTDI.4, U2.3 (IN)
VDDA: C5.1, L2.1, R1.1, U1.13 (VDDA)
VREFH: C6.1, R1.2, U1.14 (VREFH)
VREFL: C5.2, C6.2, C7.2, L1.2, U1.15 (VREFL), U1.16 (VSSA)
VREF_OUT: C7.1, U1.17 (VREF_OUT)

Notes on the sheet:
USB-Connector
ESP8266
MCU
MCU based on the amazing Teensy 3.2, developed by Paul J Stoffregen and pjrc.com.
Place RN1 as close as possible to USB-Connector!
USB_D+ and USB_D- must be routed as a differential pair. By naming them with _N and _P Eagle automatically routes both traces when placing traces in board layout. It uses the DRU and/or net class values. See EAGLE-Menu Edit->Net classes for the values in this example board
Parts of this these schematics were inspired/taken from Teensy 3.1 schematics published by Paul J. Stoffregen at www.pjrc.com.
Created 2016 for Printrbot by Phillip Schuster (www.appfruits.com)
Do not install if Teensy Bootloader Chip (MKL02) is installed!
Power Supply
Over the air updates
Micro-SD card slot
These 0 Ohm resistors (or solder blobs) allow the ESP8266 to flash the MCU without the Teensy bootloader chip. But this is just experimental. If these are installed the MLK02 may not be installed.
LCD Display and Capacitive Touch
Printer connection
Mounting Holes

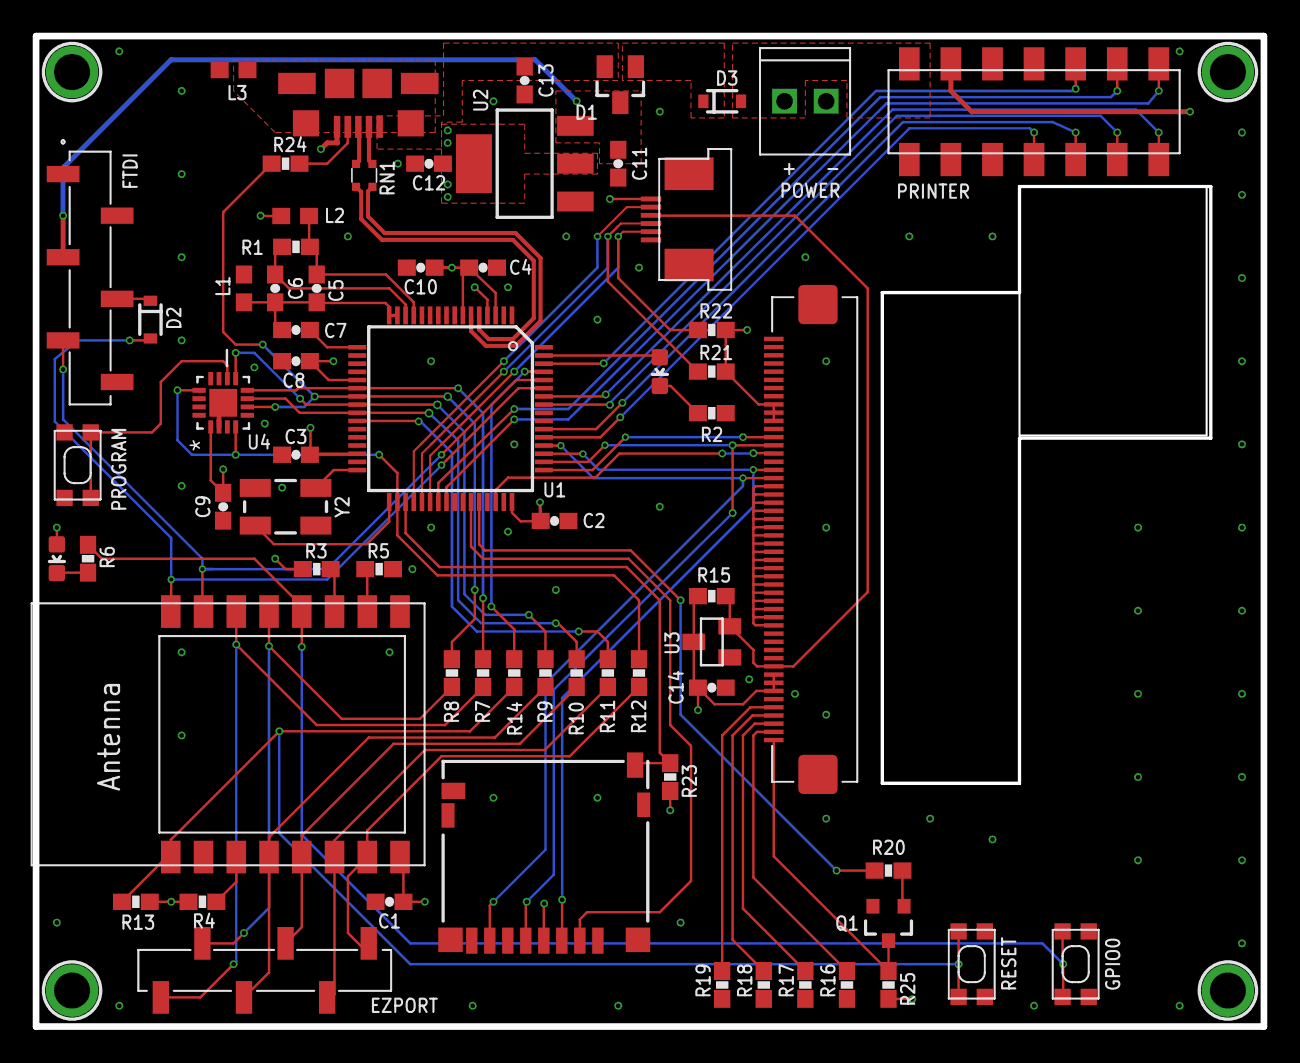
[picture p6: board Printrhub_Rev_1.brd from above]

Board: 4 copper layers, 75.0 x 60.5 mm, 70 parts (1 on the bottom side), 69 nets.

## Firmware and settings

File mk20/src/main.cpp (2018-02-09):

#include <SPI.h>       // this is needed for display
#include "framework/core/PHDisplay.h"
#include <Wire.h>      // this is needed for FT6206
#include <SoftwareSerial.h>
#include "Adafruit_FT6206.h"
//#include "SD/SD_t3.h"
#include "scenes/projects/ProjectsScene.h"

#include "framework/core/HAL.h"
#include "UIBitmaps.h"
#include "Printr.h"
///#include "Bitmaps.h"
#include "scenes/settings/DataStore.h"

// The FT6206 uses hardware I2C (SCL/SDA)
Adafruit_FT6206 Touch = Adafruit_FT6206();

//ILI9341_t3::ILI9341_t3(uint8_t cs, uint8_t dc, uint8_t rst, uint8_t mosi, uint8_t sclk, uint8_t miso)
PHDisplay Display = PHDisplay(TFT_CS, TFT_DC, TFT_RST, TFT_MOSI, TFT_SCLK, TFT_MISO);

//This is used all the time, so keep a global reference instead of building it again every time
SceneController* mainScene;

UIBitmaps uiBitmaps;

Printr printr;
DataStore dataStore;

EventLoggerClass EventLogger;


#ifdef DEBUG_USE_SOFTWARE_SERIAL
SoftwareSerial DebugSerial(DEBUG_SOFTWARE_SERIAL_RX_PIN,DEBUG_SOFTWARE_SERIAL_TX_PIN);
#endif

LED StatusLED(LED_PIN);

int globalLayerId = 0;

int globalLayersCreated = 0;
int globalLayersDeleted = 0;

int globR = 0;

int lastProjectIndex = 0;
int lastJobIndex = 0;
int totalProjects = 0;

void testImage(void)
{
    Display.fillScreen(ILI9341_WHITE);

/*    Display.drawMaskedBitmap(10,10,64,64,imageOfArrowIcon_64_64,0,0,64,64,ILI9341_BLACK,ILI9341_WHITE);
    Display.drawMaskedBitmap(10,80,32,30,imageOfCancelPrintIcon_32_30,0,0,32,30,ILI9341_BLACK,ILI9341_WHITE);
    Display.drawMaskedBitmap(10,120,24,24,imageOfWrenchIcon_24_24,0,0,24,24,ILI9341_BLACK,ILI9341_WHITE);*/

    //Display.drawBitmap(0,0,320,240,idlescreen,0,0,320,240);

    while(true) {};
}

void showSplashScreen()
{
    File file = SD.open("ui.min", FILE_READ);
    Display.drawFileBitmapByColumn(0,0,320,240,&file,0,0,320,240, uiBitmaps.splash.offset);
    file.close();

    Display.fadeIn();
}

void setup(void)
{
    //while (!Serial);
    //Initiate Status LED to be able to show some errors
    StatusLED.begin();
    StatusLED.pulse(1,false);

    // init printer pins

    pinMode(G2_RESET_PIN, OUTPUT);
    digitalWrite(G2_RESET_PIN, LOW);
    delay(500);
    digitalWrite(G2_RESET_PIN, HIGH);

    pinMode(G2_ERASE_PIN, OUTPUT);
    digitalWrite(G2_ERASE_PIN, LOW);

#ifdef DebugSerial
    {
        DebugSerial.begin(115200);

        #ifdef DEBUG_SETUP
        DEBUG_SETUP;
        #endif

        EventLogger.setLogContexts(LOG_FLOW|LOG_PRINTER);
        EventLogger.setLogLevel(LOG_SPAM);

        DebugSerial.println("============================================================================================================");
        DebugSerial.println("Debug Serial initiated");
    }
#endif

    LOG("Printrhub - LCD Controller and Hub for Printrbots!");

    if (!SD.begin(15))
    {
      Display.fillRect(0,0,320,240,ILI9341_WHITE);
      Display.setCursor(10,10);
      Display.setTextColor(ILI9341_BLACK);
      Display.println("Couldn't start SD card!");
      Display.fadeIn();

      LOG("Couldn't start SD card");
      StatusLED.on();
      while (1);
    }
    LOG("Started SD card interface");

    //Initiate communication pipeline to ESP8266
    Serial3.begin(COMMSTACK_BAUDRATE);
    //Serial3.attachCts(14);
    //Serial3.attachRts(2);

    //Pull backlight pin to turn on display backlight
    pinMode(TFT_BACKLIGHT_PWM,OUTPUT);
    //digitalWrite(TFT_BACKLIGHT_PWM,HIGH);
    analogWrite(TFT_BACKLIGHT_PWM,0);

    delay(100);

//    pinMode(7,INPUT);
//    pinMode(8,INPUT);

    Display.begin();


    //Rotate to landscape
    Display.setRotation(ILI9341_ORIENTATION_LANDSCAPE_LEFT);
    Display.setScroll(0);

    showSplashScreen();

    if (! Touch.begin(TFT_TOUCH_SENSE_PIN,40))
    {  // pass in 'sensitivity' coefficient
        LOG("Couldn't start FT6206 touchscreen controller");
        StatusLED.on();
        while (1);
    }
    LOG("Capacitive touchscreen started");

    //Display.fillScreen(ILI9341_BLACK);

    //testFont();

    //Display.setScrollArea(0,270,50);
    //Display.setScrollInsets(50,0);

    //Initiate Application
    Application.setup();

    LOG("Starting MainMenu");
    //mainController = new MainSceneController();
    //Application.pushScene(mainController);
    //wifiController = new WiFiSetupSceneController();
    //Application.pushScene(wifiController);


//    mainScene = new ProjectsScene();
//    Application.pushScene(mainScene);
}

void loop()
{
  Application.loop();
}

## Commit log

2016-01-15 fixed filament screen
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2016-01-18 Added new Display Logic System by segmenting the screen into rectangles that never overlap but fill the whole screen. This allows flicker free, fast rendering of flat interface elements and animation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
2016-01-19 Fixed memory bugs, but one bug remains causing the app to stop working after a minute.
    [Application.cpp]
2016-01-19 Switched to landscape mode and removed 16ms delay in Application loop for smoother animation.
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2016-01-22 pb marlin initial commit
    [Configuration.h, Configuration_adv.h]
2016-01-23 Added core touch handling event handling and message system. Implemented standard implementation in Views and Scene Controllers. Finalized (Bitmap)Button with "Press in, Move out" animation and deleg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
2016-01-25 Fixed a bug with unvisible layers rendered in first frame. Reactivated bitmap drawing. All parts are combined now: Layout-System and Hardware-Scrolling with cropped Bitmaps and smooth animations.
2016-01-25 auto leveling and serial bug fix
    [Configuration.h]
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2016-01-26 Made ILI9341_t3 display driver local so we can track changes that are necessary.
2016-01-26 Added clipped text rendering, text layer and label view. Had to modify ILI9341 display driver so we keep the rule that each layer is opaque (which ILI9341 font implementation is not, i.e. no backgrou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
2016-01-27 Display Driver now automatically calculates the optimum layout frame (based on the layers added to the display) and stops scrolling when the bounds are reached
2016-01-27 Added WifiSetupController with text buttons to enter a SSID (just non functional demo at the moment)
2016-01-28 fixed auto level bug
    [Configuration.h, Configuration_adv.h]
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2016-01-31 SceneControllers now control the background color for the whole screen. Added new fonts and implemented first screens of final UI design. Added virtual keyboard and scrolling "choose print job" scene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
2016-02-09 Removed Scene Stack as only one scene can be visible. Also fixes strange layout issues.
    [Application.cpp]
2016-02-29 Fixed a bug in CLI Teensy loader (old version only uploaded 50% of the code resulting strange crashes)
2016-02-29 Scrolling ends faster now by setting scrolling velocity to 0 once its lower that 0.5
2016-03-21 Added README with thoughts on components and parts for the Printrhub PCB
2016-03-21 Added a README file with info on SWD debugging and current state. Also added a few traffic captures of the SWD protocol.
2016-03-25 Firmware requires these files on the SD Card in the root folder. These are images of possible print jobs
2016-04-01 Added Printrhub PCB
    [Printrhub.brd, Printrhub.sch]
2016-04-01 Renamed Printrhub PCB to include revision. Each major revision gets their own file
    [Printrhub_Rev_0.1.brd, Printrhub_Rev_0.1.sch]
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2016-04-29 Turn off display leds before scene changes and turn it on again when scene has been finished drawing. This looks better as it's not visible how the scene is built up. Tried a little animation using P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
    [Application.cpp]
2016-04-29 Added scroll insets that allow for a steady sidebar combined with hardware scrolling. Modified existing scenes like main menu and choose print to use the new API and layout.
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2016-05-04 Added CLion project files for PlatformIO build system, added vertical text layer and missing touch library. Also added sidebar controller and first structures to implement final UI.
    [Application.cpp, main.cpp]
2016-05-06 Reworked large portions of UI controls to support final UI design. Added masked bitmaps that allow for very slim memory footprint for monochrome but colorful images. Added splash screen showing the P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
    [main.cpp]
2016-05-06 Reworked ColorTheme to a few easy to access and read colors that can easily be changed. Reworked most controls so they use standard colors per default and removed color setup code from scene controll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
    [Application.cpp, main.cpp]
2016-05-09 Fixed conflicts with existing libraries SD and StackArray by removing them from PlatformIO build stack (see platformio.ini) as we have custom ones added and refactored firmware source code in differe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
    [Application.cpp]
2016-05-09 Added support for icons to LabelButton. They are shown left of the label text. Icon and text are separated 10 pixels are center aligned in the available button space.
2016-05-09 Added ConfirmSceneController that shows an "Are you sure" message with two buttons YES and NO.
2016-05-09 Added Debug method to layout system that shows each step during the layout process by rectangles drawn on screen and needs a tap after each step to proceed with the next step. This way you can trigge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
2016-05-09 Added (first page) of Settings Controller. Pressing the Wifi Settings button proceeds with other scenes.
2016-05-09 Added a known bug comment to display code. Will fix it later but it's currently not needed by current firmware UI.
2016-05-10 Displays shows error message at startup if SD card cannot be initialized
    [main.cpp]
2016-05-10 Disabled optimized Teensy SD card library as it has problems rendering larger SD bitmaps.
2016-05-10 Added support for a fixed background layer in a layout that is drawn first and all following layers are drawn over it. This effectively turns off the layout system (for the current draw cycle).
2016-05-10 Added PrintStatusSceneController and added it to startup code so it shows up first
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2016-05-11 Reimplemented hardware based scrolling with a static sidebar and local coordinate system for fixed and scrolling parts of the display. Added the concept of static and fixed layers, cleaned up some fu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
    [Application.cpp, main.cpp]
2016-05-11 Handle situation where finger touches control but then is moved for scrolling. Currently the view captured the touch and did not release it. If the touch control ist not handling move events the scen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
2016-05-11 Added scroll snapping to settings view controller. Current code does not allow for snapping with speed (i.e. snap at a later slot and not only the next).
2016-05-12 Added scene for printjobs using the new sidebar scrolling. Works fine, however there are graphical glitches due to slower rendering of SD card images when scrolling really fast.
    [main.cpp]
2016-05-13 Fixed graphical glitches when scrolling projects by introducing a switch for auto layout. This turns off auto layout completely and allows for faster refresh rates when the scenes are opaque (i.e. al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
2016-05-13 Reworked scene code a bit. SidebarSceneController now handles bottom left action button (in sidebar) and calls a function that the subclass can handle.
2016-05-13 Added physically based scrolling code (realistic acceleration and deceleration) with snapping and flicking multiple slots at once. Fixed a lot of bugs and fixed a few other smaller bugs. Added a lot 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
    [Application.cpp]
2016-05-13 Added print button to print job selection and implemented basic application flow from selecting a job, pausing it, resuming and so on
2016-06-21 Implemented firmware update of MK20 through ESP8266 over the air. ESP8266 downloads firmware and writes it to the MK20 via SWD and program longword. That is very slow, but works reliable. Contains co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
2016-06-24 Added application framework for ESP8266 firmware like the one in the Printrhub MK20 firmware. I.e. having a global Application class that handles different modes that are pushed on the stack.
2016-06-30 Added Revision 0.2 of Printrhub PCB
    [Printrhub_Rev_0.2.brd, Printrhub_Rev_0.2.sch]
2016-07-09 Fixed a small bug in Rev 0.2 of the Printrhub PCB
    [Printrhub_Rev_0.2.brd, Printrhub_Rev_0.2.sch]
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2016-07-12 Implemented file download communication between MK20 and ESP and increased baud rate. Activated flow control which does not really make a difference for now.
2016-07-13 Implementation of file downloads with current CommStack architecture. Problem is it blocks the whole device and is not very reliable. Will switch to a more packet orientated style.
    [Application.cpp]
2016-07-13 Added PubNub Logger to ESP but does not work reliable. Completely rewrote communication stack to only send junks of data and separated by a package marker (PacketSerial). Works fine, although subsequ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
    [Application.cpp, main.cpp]
2016-07-13 Fixed a few minor bugs.
    [Application.cpp]
2016-07-19 Added some basic flow control test to allow for display updates while receiving data but does not work at the moment (mostly commented out)
    [Application.cpp]
2016-07-25 Added system for blocking communication between MK20 and ESP while display is updated to prevent loss of data. Some sort of flow control.
    [Application.cpp]
2016-07-26 Refactored Responses to allow for sending a successful (ResponseSuccess) or failed (ResponseFailed) Response without adding another byte to the header.
    [Application.cpp]
2016-07-26 Reworked ESP part of file download to wait for a response before sending the next package. Together with the new ResponseSuccess/ResponseFailed system should increase reliability when downloading fil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
    [Application.cpp]
2016-07-28 Modified FT6202 touch screen driver to improve performance while checking for touches. Reading from the FT6202 is quite slow via I2C but FT6202 has a special mode where interrupt pin can be set to be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
2016-07-28 Added a signal (pin 13) to show what the ESP is doing in the Logic Analyzer. Allows for better optimizations.
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2016-08-01 Added a LED class with a few convenient functions to turn it on, off or pulse it with a certain frequency. Added some code to use the LED as some kind of error reporting. When it turns on there is an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
    [Application.cpp, main.cpp]
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2016-08-01 Fixed a bug with wrong pin assignment on rev 0.2
    [Application.cpp]
2016-08-01 Removed interrupt based data flow handling and replaced with direct reads of GPIO.
2016-08-01 Fixed some pin assignments on ESP for hardware revision 0.2
2016-08-09 starting final branch
    [Configuration.h, Configuration_adv.h, Printrhub_Rev_0.1.brd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]
2016-08-10 Added Revision 0.3 work in progress. Modified dimensions and display placement for final Simple design and rerouted traces accordingly.
    [Printrhub_Rev_0.3.brd, Printrhub_Rev_0.3.sch]
2016-09-02 added pin init for G2 Reset and Erase pins
    [main.cpp]
2016-09-04 Updated to latest version of 0.3. This is the one that went to the board house.
    [Printrhub_Rev_0.3.brd, Printrhub_Rev_0.3.sch]
2016-09-04 Added support for Rev 0.3 when R8 is installed (R8 pulls RESET_B low, must be pulled high for the MK20 to start)
    [Application.cpp]
2016-09-06 Rev 0.4 of Printrhub. Moved touch controller connector to correct location and modified a few traces to make room. Also removed SCL1 and SDA1 from expansion port and added async serial used for CommS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
    [Printrhub_Rev_0.4.brd, Printrhub_Rev_0.4.sch]
2016-09-06 Readded SCL1 and SDA1 (so this version is committed, too).
    [Printrhub_Rev_0.4.brd, Printrhub_Rev_0.4.sch]
2016-09-06 Added pull-up and pull-down resistors for PRINTER_RESET and PRINTER_ERASE signals. Replaced plated mounting holes with larger holes (without plate). Moved a few parts for nicer layout.
    [Printrhub_Rev_0.4.brd, Printrhub_Rev_0.4.sch]
2016-09-08 Changed drill size from 3.2mm to 2.9mm
    [Printrhub_Rev_0.4.brd, Printrhub_Rev_0.4.sch]
2016-09-08 Moved display 0.45mm to the right (from component side), moved some traces to make space and moved test points a bit to make them more centered above the SD card slot.
    [Printrhub_Rev_0.4.brd]
2016-09-13 added g2 reset and erase pins and splash screen that is loaded from ui file
    [main.cpp]
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2016-09-21 Fixed various bugs when scrolling by adding a scroll offset that moves the visible "action" to the other side of the screen making it harder for the eye to see it. Also added a delay of 5 millis betw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
2016-09-21 Fixes a scrolling bug when a lot of slides are available in project view. It could happen that scrolling velocity got so high that animation could not keep up causing strange effects and graphical er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
2016-09-22 Fixed a bug in PreheatExtruder. C-Strings must be strcompare'd as there is no default operator for const char. After this fix I was able to do a complete filament change complete with working progres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
2016-09-23 Fixed bugs in calibrate scene. Works fine now.
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2016-09-27 CommStack TaskIDs are now scoped enumeration meaning that enum values aren't defined in global scope meaning less confusing error codes when compiling and better code structure. (+1 squashed commit) 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
    [Application.cpp, web_server.cpp]
2016-09-27 Changing progress bar value required a full relayout due to setFrame called on it's track layers. This is not necessary as the progressbar as a whole does not change in relation to other views, thus 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
2016-09-27 Reworked file downloads. On ESP side the fetch request on the server is sent to MK20 using a JSON package which in turn starts the DownloadFileController which shows a progress bar and starts Downloa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
    [Application.cpp, errors.h, web_server.cpp]
2016-09-27 Added job downloads and reworked JobsScene to be a bit more MVC, i.e. a Job structure holds the job info and ImageView just shows them. When the button is pressed the correct Job is selected from the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
2016-09-28 updated project index
    Added revision info to project and job (in project index file), and
    number of times job has been printed. Also updated Job and Project
    status scenes to be able to read new index files correctly.
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2016-09-29 Added a custom WiFi driver in order to speed up downloads - but didn't help yet.
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2016-10-10 fixed print button implementation
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2016-10-13 Completely reworked CommStack. Previously separated packets for headers and data are now combined into one. This is much more reliable as it's not necessary anymore that packets come in in the right 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
    [Application.cpp]
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2016-10-13 Pimped background jobs and fixed some bugs.
    [Application.cpp]
2016-10-13 Fixed a possible bug in ARM flashing
2016-10-13 Fixed a bug with new modal system that prevented error message to be shown
    [Application.cpp]
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2016-10-13 adding finish print scene and few small fixes
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2016-10-16 Solved issues with response parsing from printer
    [Application.cpp, Printr.cpp, main.cpp]
2016-10-16 fixed issue where buttons stop responding on project and job scene (with only one item) after swipe
2016-10-17 Modified Printer class to do all communication with printer asynchronous even for setup, startup and clearance GCode.
    [Printr.cpp]
2016-10-17 Show WiFi info when WiFi settings have been changed. Fixes #9
    [Application.cpp, MK20.cpp, web_server.cpp]
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2016-10-24 Bugfix in MemoryStream fixes bug with printer stopping to print after initial startup code is sent.
2016-10-24 Fixed a bug with Display buttons sometimes not responding.
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2016-10-24 Modified Printr class to send multiple lines before waiting for a response (corresponds to g2 documentation of bursting in 4 lines at startup). Comments are skipped now. Added massive logs to show er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
    [Printr.cpp]
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2016-10-25 Added a maintenance method for formatting SPIFFs in case device makes problems this could help.
    [web_server.cpp]
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2016-10-25 Removed old printrCallback which is now replaced with a more formal class interface.
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2016-10-26 Tried to fix issues with Filament management
    [Printr.cpp]
2016-10-26 fixed close button to allow it to exit current scene
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2016-10-27 Fix bug with too long 0 in calibrate scene. Fixes #19
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2016-10-27 Fixed the bug in calibrate scene with corrupted hotend offset text. Requires an updated ui.min on SD card.
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2016-10-27 Replaced Printr class with latest version from GoodPrintr
    [Printr.cpp]
2016-10-28 Added onDidAppear to allow the scene to adjust scroll position before it's displayed. Jumping back from Jobs now shows the corresponding project in project browser. Fixes #26
    [Application.cpp]
2016-10-28 reset _progress to 0.0 on start of new job
    this issue has been preventing new job to from starting after
    successful print
    [Printr.cpp]
2016-10-28 Modified BitmapView for optimized application flow - also fixes possible memory leak when changing images.
2016-10-28 Fix bug with nan scroll velocity (again - see 2016-10-25 commit)
2016-10-28 Fixed a bug with load/unload filament. Fixes #28
2016-10-29 adding missing images for filament load/unload screen and other small gui tweaks
    bug #22
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2016-10-31 fixed issue with Print cancel screen where it would lock up after trying to cancel print
    [Printr.cpp]
2016-10-31 prevent new project download while printer is busy printing
    Print status scene is now modal, which prevents any new screen from
    interrupting it (unless it is on button press). This fixes bug #30
    [Application.cpp]
2016-10-31 adding blank images for sidebar and sidebar icon since setting them to NULL causes screen to not load
    after scene optimizations, something changed in core libraries that is
    causing scene not to load if sidebar icon and image are not set. To
    prevent that I created two blank icons that can be used where we don’t
    want to show button or sidebar. This is a hack and not an actual fix
2016-10-31 fixed bug #23
    removed stat3 check that was causing print to finish before it starts.
    Stat 3 means that G2 queue is empty, not that print job is finished,
    and it can happen in the middle of the job (if there are a lot of small
    moves that get consumed faster then queue can be populated)
    [Printr.cpp]
2016-11-01 Fixed a bug in DownloadFileToSDCard which did not send the last packet again when it was asked to do so in ResponseFailed (CommStack error) resulting in corrupted project index files when downloaded 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
2016-11-01 Updated errors.h file on MK20 side
    [errors.h]
2016-11-01 Print flag is now reset when print is stopped
    [Printr.cpp]
2016-11-01 Added Set Password dialog, virtual keyboard and CommStack event handling. Setting an empty password clears it. Fixes #18
    [Application.cpp]
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2016-11-01 Removed Serial debug logs when flashing ARM device and replaced with EventLogger.
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2016-11-01 Fixed a bug when triggering manual MK20 firmware without providing an URL for download
    [web_server.cpp]
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2016-11-03 Added special production ESP codepath. Uploading the data folder with UPLOADFS target will make ESP to reset its config (EEPROM) and flashes MK20 with firmware uploaded into /firmware/ directory. #35
    [config.cpp]
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2016-11-06 Removed special progress bar handling after printer is stopped. This did not work and introduced other bugs. Fixes #37
    [Printr.cpp]
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2016-11-09 added startListening and stopListening methods
    this can be used when we want to listen for the printer responses, and
    to stop printer from sending anything back to hub when we are not
    listening for events. It looks like this also fixed remaining issues in
    bug #36 and #32 where download was failing while printer hotend was hot
    (and sending messages back to hub)
    [Printr.cpp]
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2016-11-09 when changing filament, push the plastic down first 5 mm, then start retracting
    this solves the issue when changing filament where tip of the filament
    would swell up and not allow user to pull it out of the extruder
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2016-11-09 removed prompt after the print and replaced it with simple message and done button
2016-11-09 fixed graphic position and added feed rate override when removing filament...
2016-11-10 fixed issue with invalid material data when new material library is sent to printer and immediately selected without scrolling to other screens....
2016-11-10 change priming sequence to extruder a bit more plastic to make sure head is primed correctly
    [Printr.cpp]
2016-11-23 Added README files and cleaned up folder structure. Added Rev 0.1 PCB and Copper files for Rev 0.4.
    [Printrhub_Rev_0.3.brd, Printrhub_Rev_0.3.sch, Printrhub_Rev_0.4.brd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]
2016-12-10 missing IdleView.h causing compile error. since IdleSceneController isn't being used, removing it.
    [main.cpp]
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2017-02-13 fixed bug with json not parsing due to max attribute not set on readStringUntil when parsing json from job file
    max value by default is 120 and average string size is ~150 characters
    which was causing json parser to fail due to string being cut off
    [Printr.cpp]
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2017-02-24 Mac address is now displayed in Wifi setup HTML page. Fixes #9
    [web_server.cpp]
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2018-02-09 Fixed a compilation bug with characters in keyboard that don’t fit in a char.

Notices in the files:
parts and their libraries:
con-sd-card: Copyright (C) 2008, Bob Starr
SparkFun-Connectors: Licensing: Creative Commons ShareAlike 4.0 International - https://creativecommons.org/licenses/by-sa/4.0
